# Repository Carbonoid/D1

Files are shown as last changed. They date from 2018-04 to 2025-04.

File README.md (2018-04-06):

## Carbonoid D1
Repository for the Carbonoid D1 Delta Printer

During the development phase and countless optimization iterations 4 machines were built:

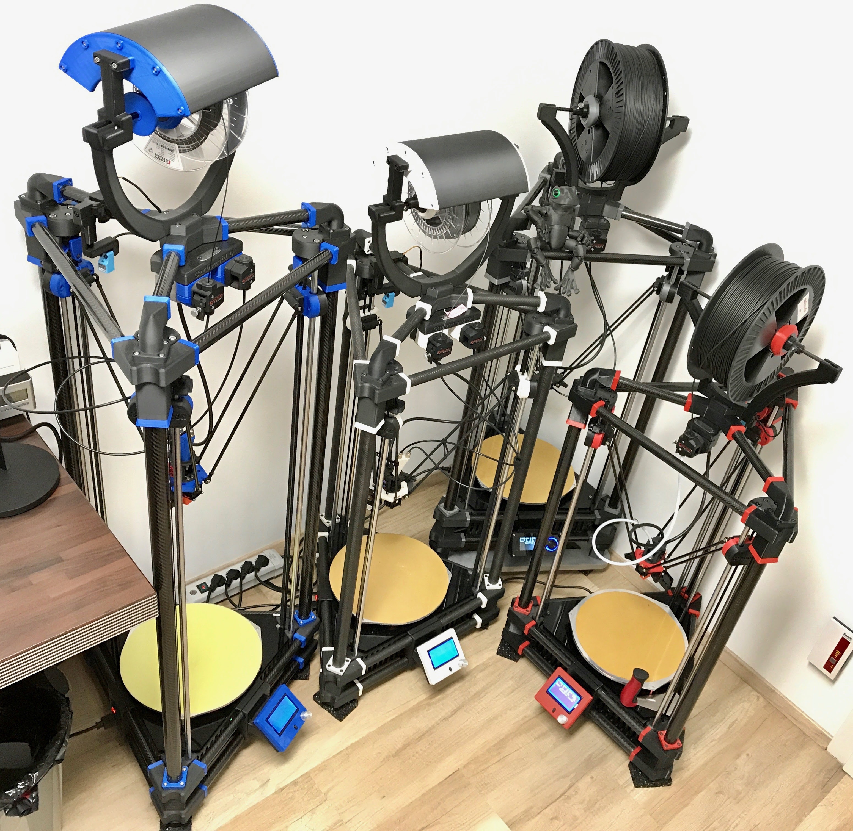
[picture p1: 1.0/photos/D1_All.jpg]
Carbonoid All-stars


The single extrusion machine #0002 is equipped with a Flex3Drive G4 extruder:

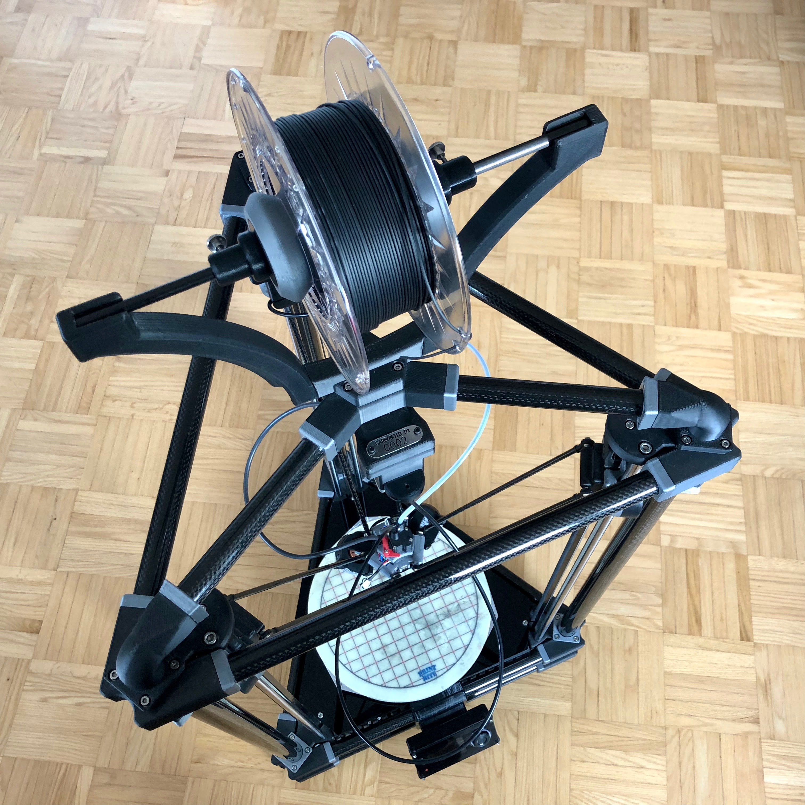
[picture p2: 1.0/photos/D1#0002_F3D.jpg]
Carbonoid D1 #0002 with Flex3Drive extruder


Machine #0004 uses a DuetEthernet and a PanelDue:

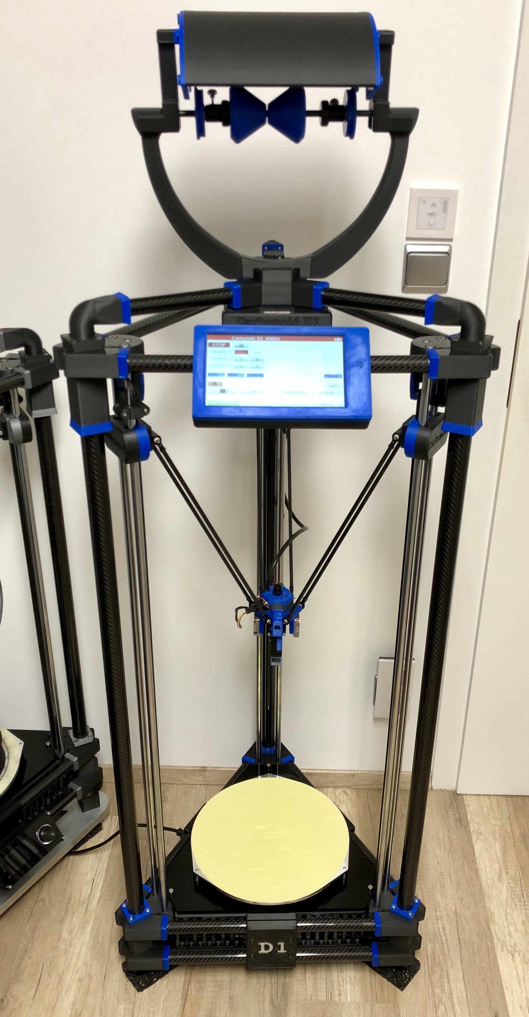
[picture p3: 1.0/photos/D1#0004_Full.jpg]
Carbonoid D1 #0004 Overview


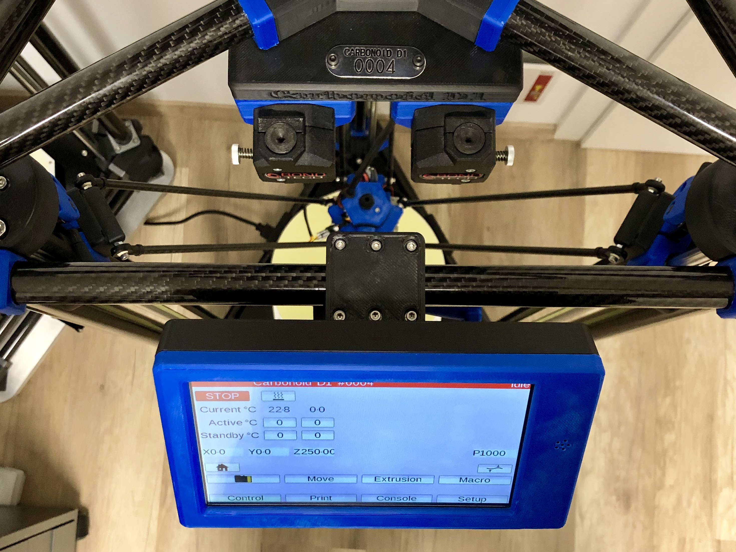
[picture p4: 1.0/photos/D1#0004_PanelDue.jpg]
Carbonoid D1 #0004 Panel Due


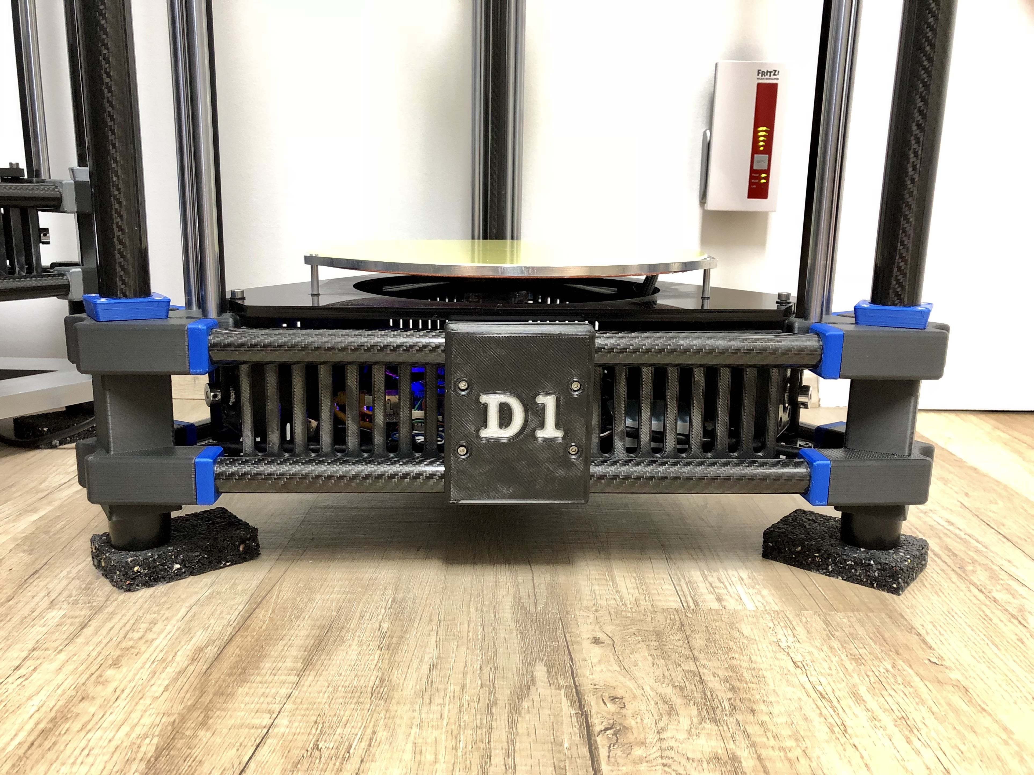
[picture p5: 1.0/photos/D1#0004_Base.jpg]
Carbonoid D1 #0004 Base


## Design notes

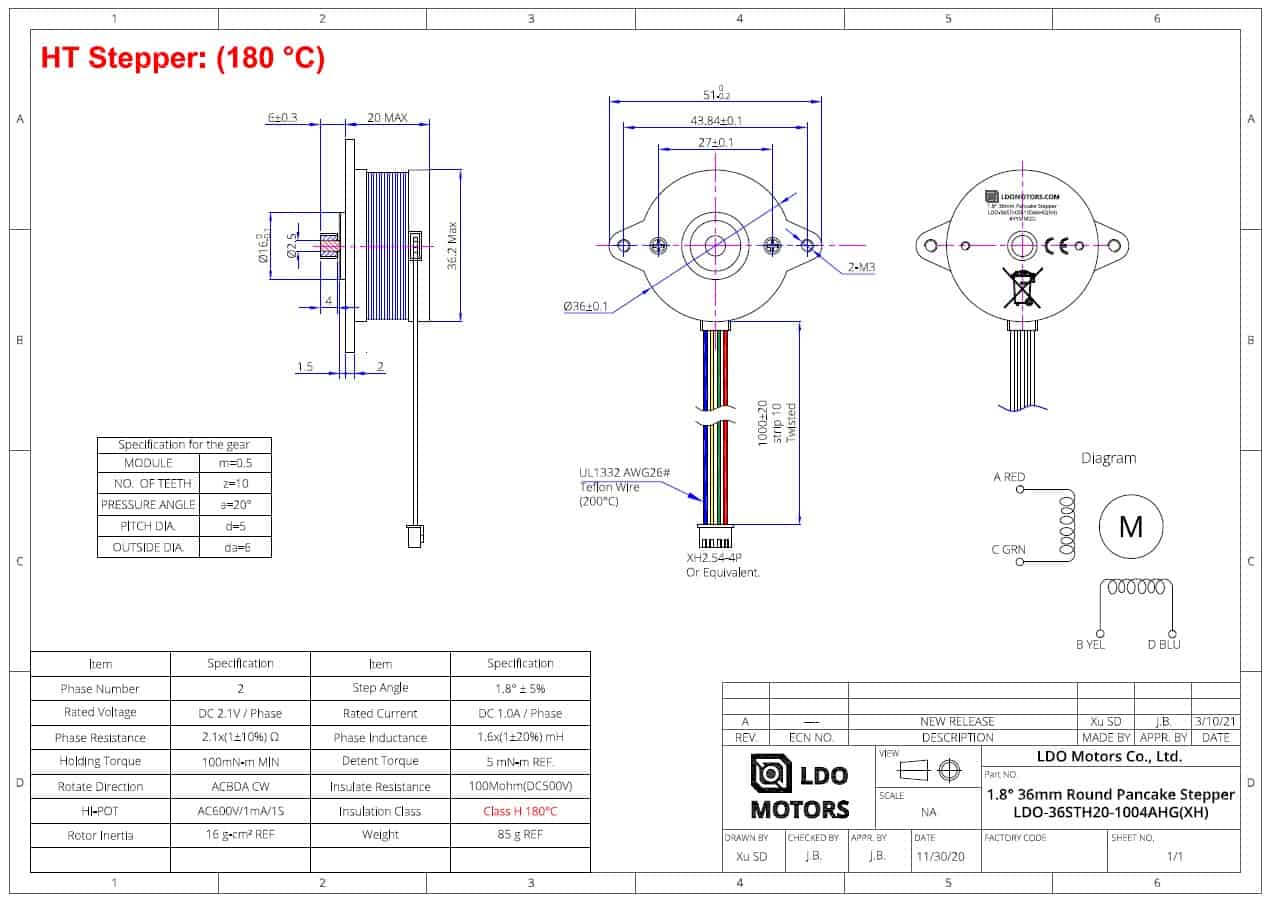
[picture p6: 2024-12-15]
1.0/hardware/drawings_pinouts/Datenblatt_LDO-Motor.jpg

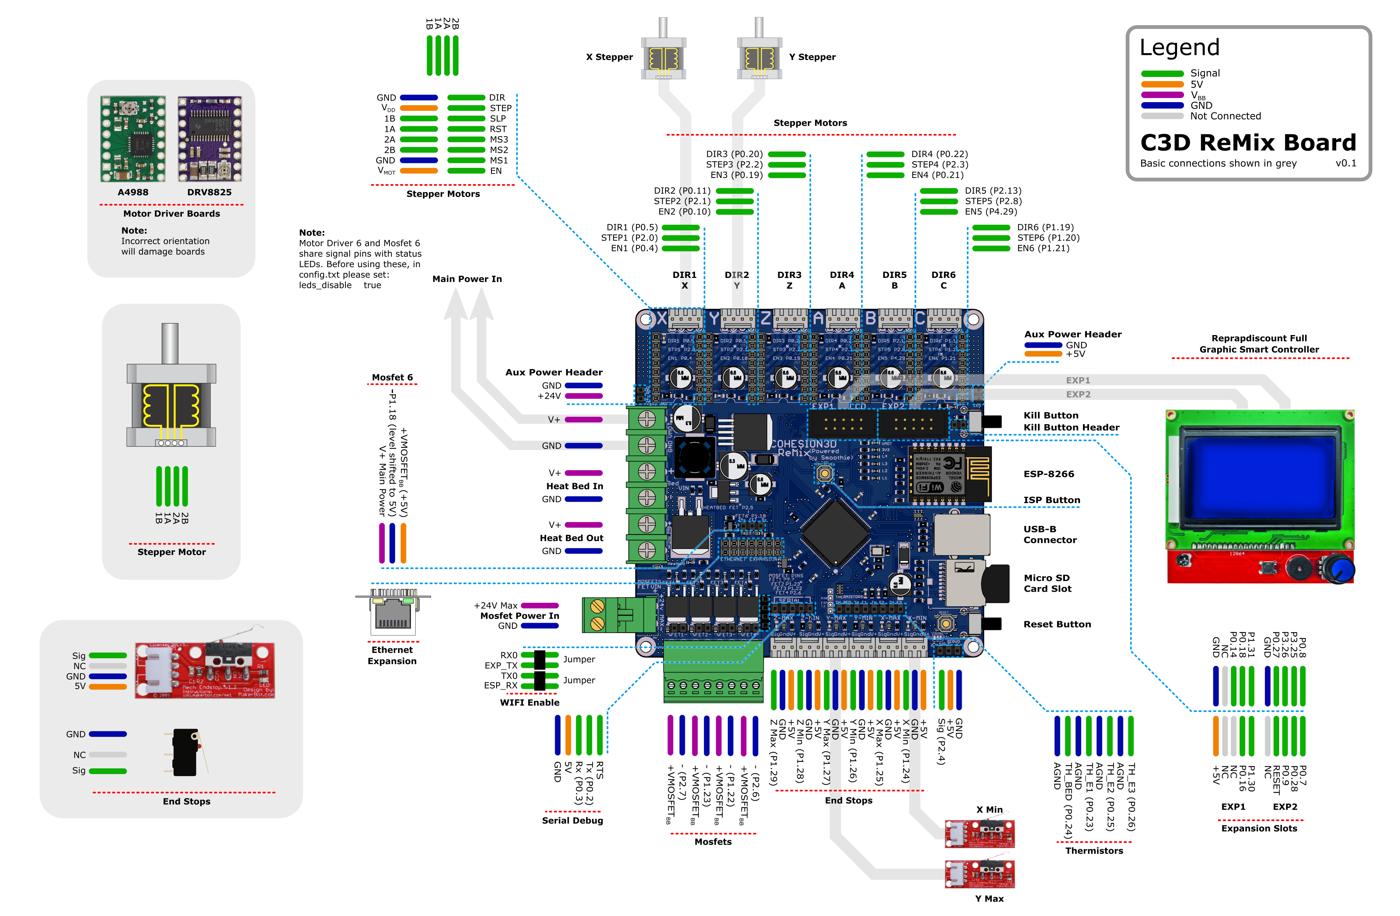
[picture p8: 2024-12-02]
1.0/hardware/drawings_pinouts/C3D_Remix_Pinout.png

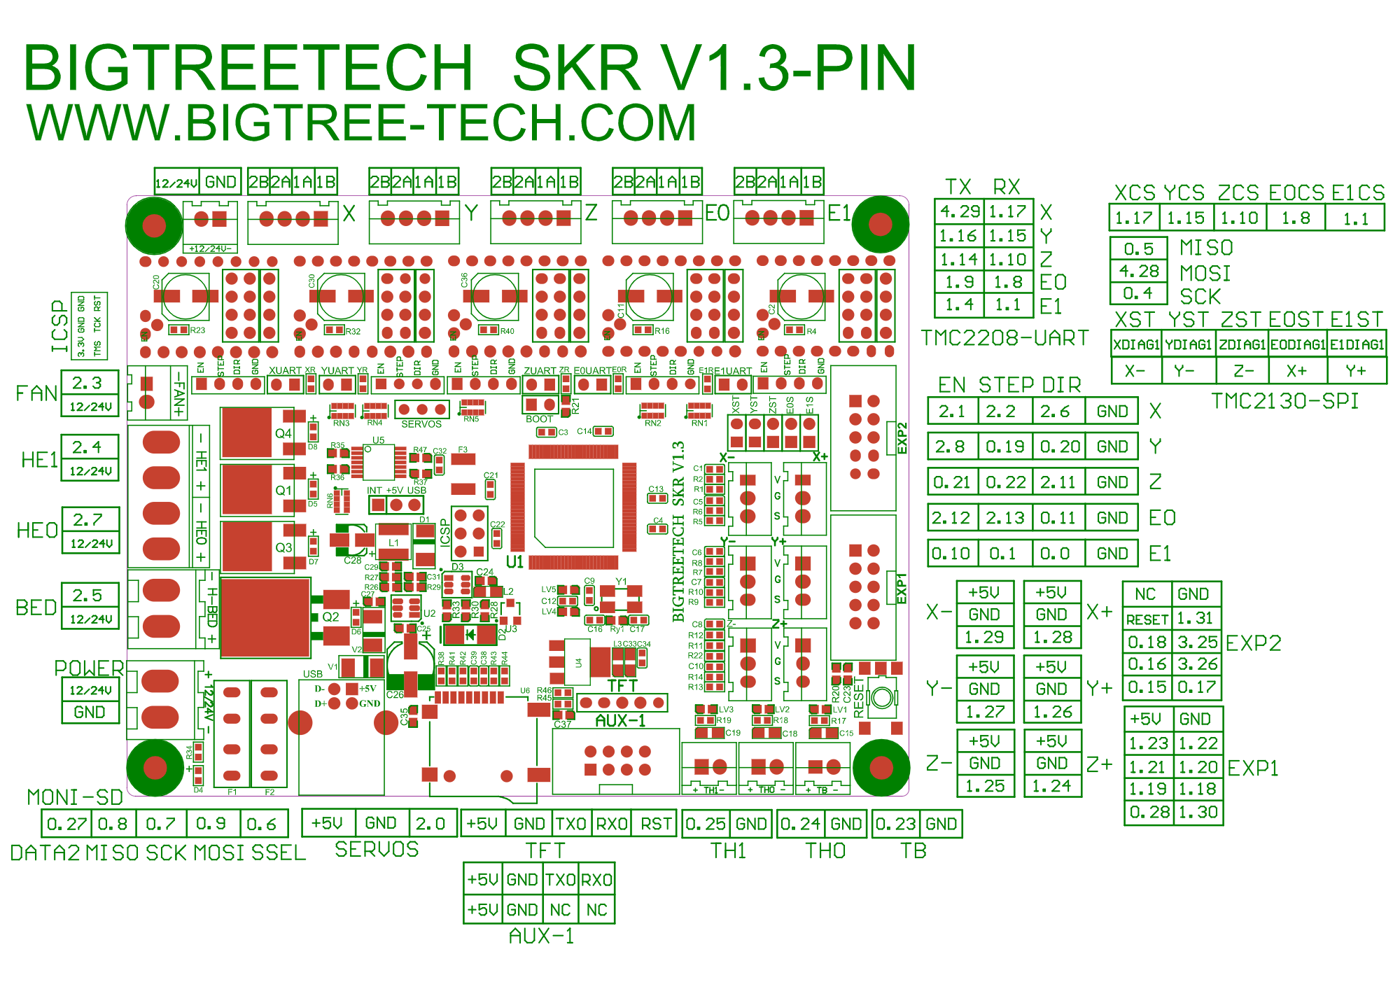
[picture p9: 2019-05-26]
1.0/config_klipper/#0001/BTT_SKR_v1.3_XYZE_TMC2100_F3D_G5/GLCD_Cable/SKR V1.3 Pinout.png

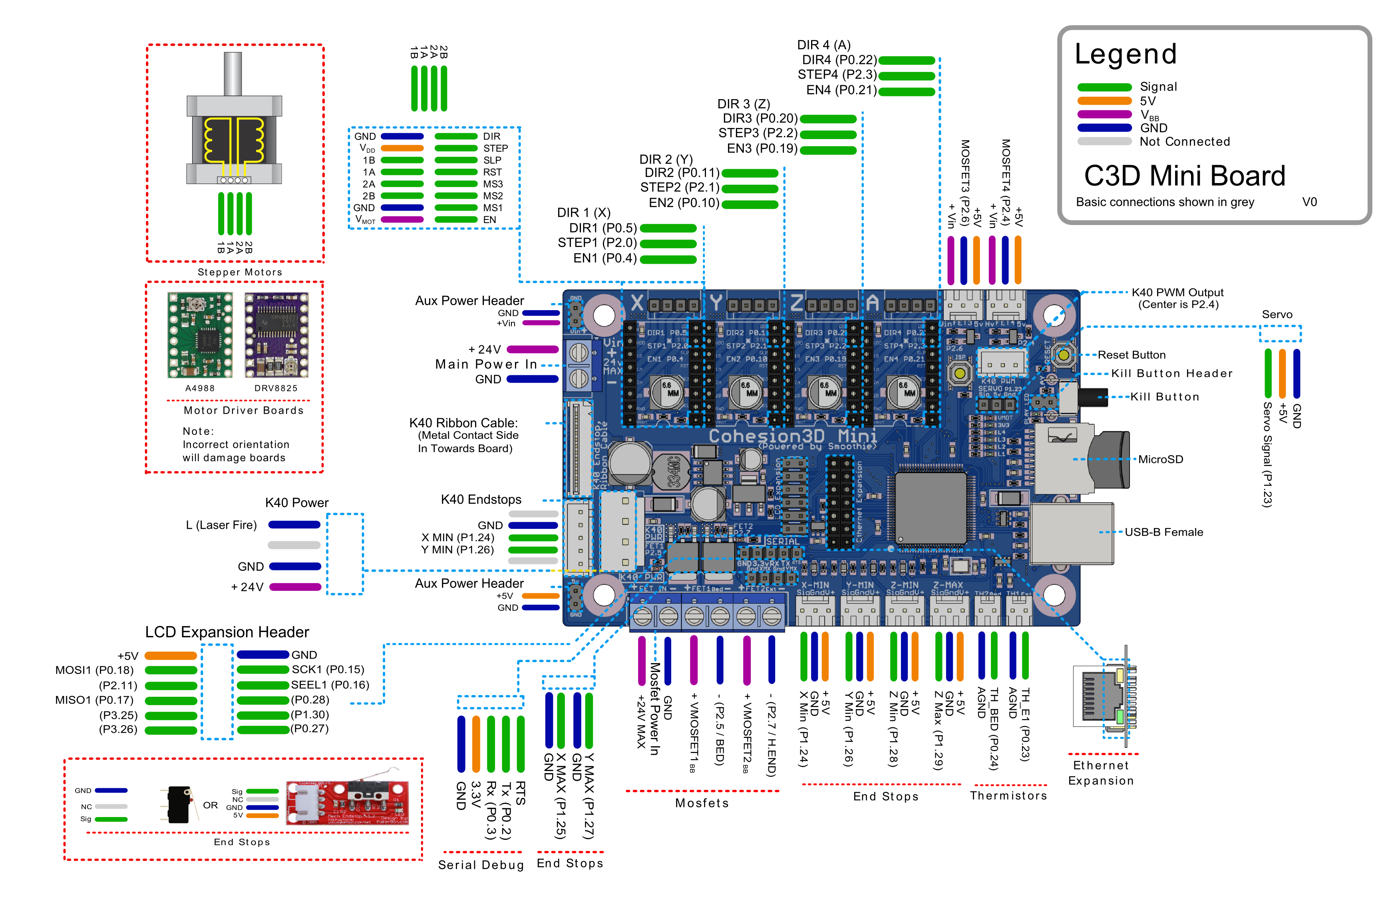
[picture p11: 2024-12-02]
1.0/hardware/drawings_pinouts/C3D_Mini_Pinout.png

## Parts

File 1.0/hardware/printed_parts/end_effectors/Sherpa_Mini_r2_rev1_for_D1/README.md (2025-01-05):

## Sherpa Mini - Release 2 - Carbonoid Specific Changes

No other changes than the ones below were made. The copyright to these files belongs to ANNEX-Engineering: https://github.com/Annex-Engineering/ANNEX-Engineering-License-Agreement

+ Diameter of the 5 heat-set brass inserts modified to 3.8 mm, to match the M3 insert type (Tappex) used on the Carbonoid D1 printer design.

## Sherpa Mini - Release 2:

This release adds support for Bondtech's RIDGA v2 in addition to numerous tweaks and updates to make the extruder easier to work on and more reliable than ever. 

## Changelog

+ Bondtech RIDGA v2 compatibility (R2 RC1 and newer)
+ Bondtech insert support
+ Stronger and stiffer idler arm
+ Increased clearance between idler arm and core
+ Minor fixes and adjustments in preparation for upcoming upgrades

+ Core housing and rear housing need to be reprinted if upgrading from Release 1
+ Updated idler arms are backwards compatible with Release 1 and Release 2 RC1

## FAQ
For Material Requirements, Print Settings and How to Interpret the file naming structure, please see: "Print_Settings_and_File_Key.txt"

The BOM and Sourcing Guide for this product can be found here: https://docs.google.com/spreadsheets/d/1O3eyVuQ6M4F03MJSDs4Z71_XyNjXL5HFTZr1jsaAtRc/edit?usp=sharing

## Product Info
This is the Sherpa Mini Extruder, a ground up design developed by Anlin and the team at Annex Engineering. It's a dual geared hobbed filament extruder designed for use with any printer. It features a gear driven design to provide torque while being able to be near silent. You must perform your own tuning to get the best results.

A Pinion Equipped Pancake Stepper is required for this Release.

Our discord server can be found here: 

Join me on Discord (https://discord.gg/MzTR3zE)

Please only use GitHub Issues for repo and file related problems. For general design related questions and technical support please visit our Discord server.

Image of Sherpa Extruder

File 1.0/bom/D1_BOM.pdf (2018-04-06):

Carbon tubes
Alternative 1 (D1 standard): 3x 30x26x863 mm Alternative 2 (D1 extended): 3x 30x26x1063 mm 9x 22x18x450 mm
3x 22x18x225 mm
6x 6x4x348 mm
Item | Description | Source | Qty.
GT2 Kit | 3x 2m GT2 Zahnriemen, 6x GT2 20 Pulley | www.ebay.de | 1
Shoulder bolts | GMSB4-20 / 34-02-E6 | www.misumi.de | 3
Set Screws | M3x 30 10x | www.ebay.de | 1
Extruder | 1.75 mm Bondtech QR | www.bondtech.se | 1
Silicone bed heater + SSR | 230V / 480W Silikonheizmatte + 230V / 10A SSR www.filafarm.de | 1
PSU | Meanwell RS-100-24 24V/108W | www.ebay.de | 1
Cast aluminium heated bed | 6mm Cast aluminium custom made | http://www.bam-maschinenbau.de | 1
Bearings | F624ZZ | www.ebay.de | 10
Bearings | 604ZZ | www.ebay.de | 4
Alternative 1: Controller / Display | Azteeg X5 mini, mini Viki, 4x SureSepr SD2210 | www.panucatt.com | 1
Alternative 2: Controller / Display | Cohesion3D Remix, GLCD, 4-6x TMC2100/2208 (2208 for xyz and 2100 for extruder works great) www.panucatt.com | 1
Alternative 3: Controller / Display | Cohesion3D mini, GLCD, 4x TMC2100/2208 (2208 for xyz and 2100 for extruder works great) www.panucatt.com | 1
Alternative 4: Controller / Display | Smoothieboard 1.1, GLCD Display | http://smoothieware.org/getting-smoothieboard1
Alternative 5: Controller / Display | DuetEthernet or Wifi, Panel Due 7" | https://www.duet3d.com | 1
Raspberry Pi 3 B+ | Optional but highly recomended | https://www.raspberrypi.org/products/ | 1
SN04 Sensor | SN04-N Sensor | www.aliexpress.com | 1
Filament | 5kg Green-TEC | www.extrudr.com | 1
Ball joints | KBRM-03 M4 MH Igubal ball joint | www.igus.de | 12
Alternative 1: Bushings | 6x Igus RJUM-11-12 | www.igus.de | 6
Alternative 2: Bushings | 6x sintered bronze bushing 16x12x25 mm | www.ebay.de | 6
M2.5 Inserts | KVT M2.5 MULTISERT | http://www.kvt-fastening.de | 6
M3 Insert | KVT M3 MULTISERT | http://www.kvt-fastening.de | 50
M4 Insert normal | KVT M4 MULTISERT | http://www.kvt-fastening.de | 100
M4 Insert long | KVT M4 long MULTISERT | http://www.kvt-fastening.de | 100
M5 Insert | KVT M5 Insert | http://www.kvt-fastening.de | 10
NEMA17 | 0,9° LDO-42STH47-1684MAC.pdf | http://ldomotors.com | 3
Alu Spacer 20mm | Aluminium spacer 20mm | www.aliexpress.com | 3
Alu Spacer 40mm | Aluminium spacer 40mm | www.aliexpress.com | 6
Alternative 1: Linear Rod | 6x 800x12 mm with M6 Threaded Ends | www.dold-mechatronik.de | 1
Alternative 2: Linear Rod | 6x 1000x12 mm with M6 Threaded Ends | www.dold-mechatronik.de | 1
Microswitch | For enstops and alternatively for bed probe | www.ebay.de | 4

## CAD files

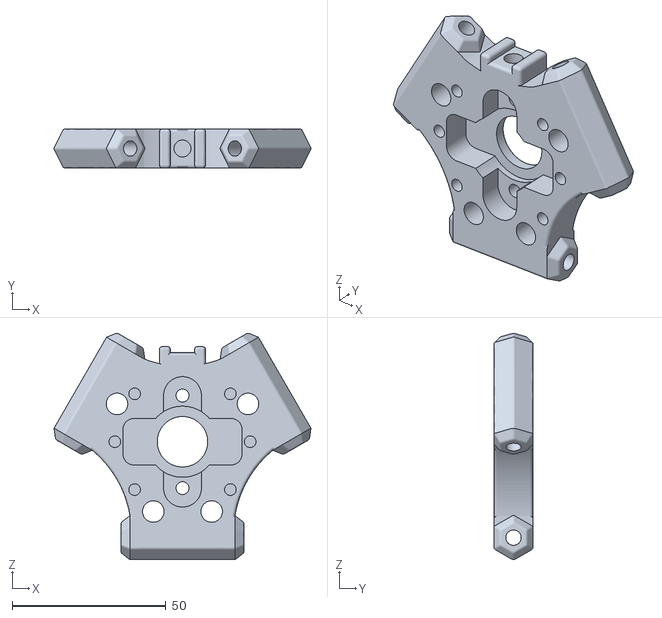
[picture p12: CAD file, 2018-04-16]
1.0/hardware/printed_parts/end_effector_v3.5/end_effector_v3.5.stl
83.5 x 12.7 x 73.6

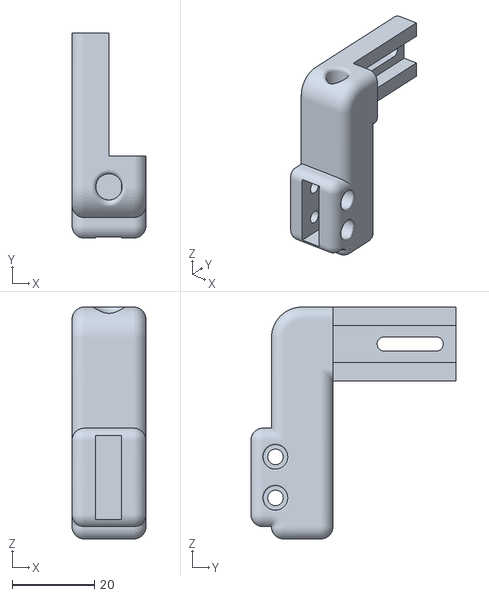
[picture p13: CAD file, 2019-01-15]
1.0/hardware/printed_parts/end_effectors/bed_probe_arm_since_v5/bed_probe_arm_lower_microswitch.stl
18.0 x 50.0 x 56.5

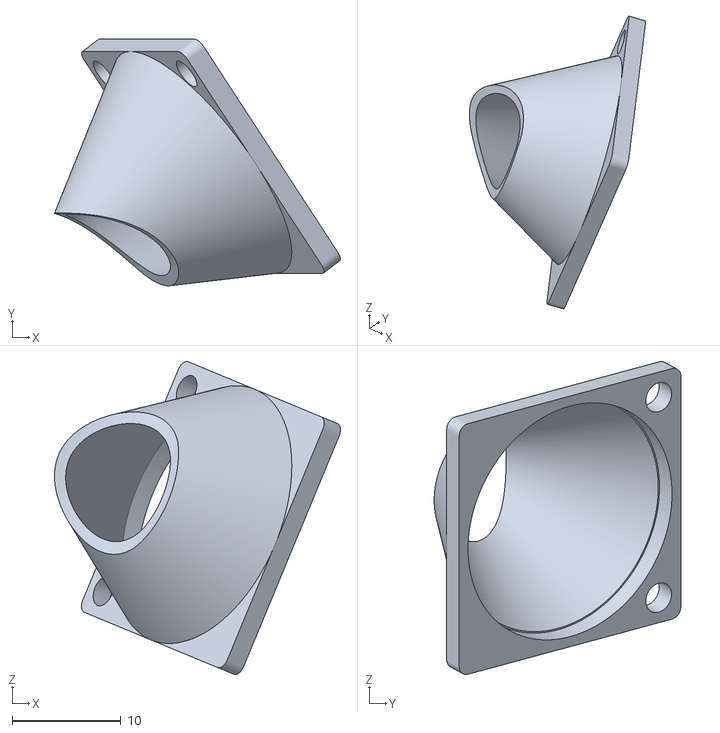
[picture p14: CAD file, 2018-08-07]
1.0/hardware/printed_parts/end_effectors/filament_cooling/25_mm_fan_duct/25_mm_fan_duct.stl
26.4 x 22.7 x 28.8

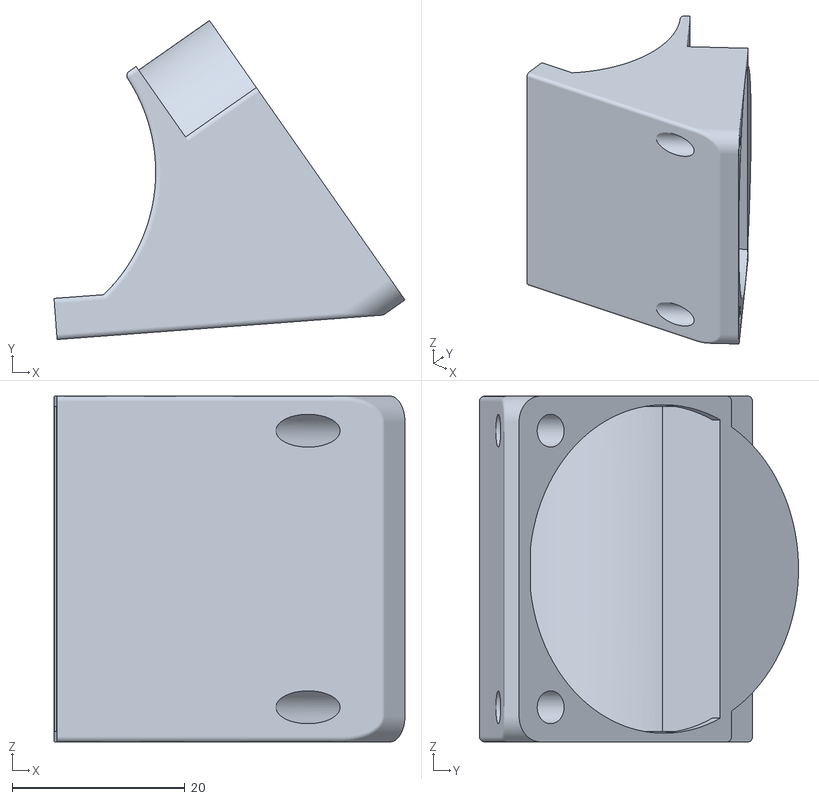
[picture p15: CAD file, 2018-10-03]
1.0/hardware/printed_parts/end_effectors/filament_cooling/40_mm_fan_ducts/40_mm_fan_duct_v5.stl
40.6 x 36.9 x 40.0

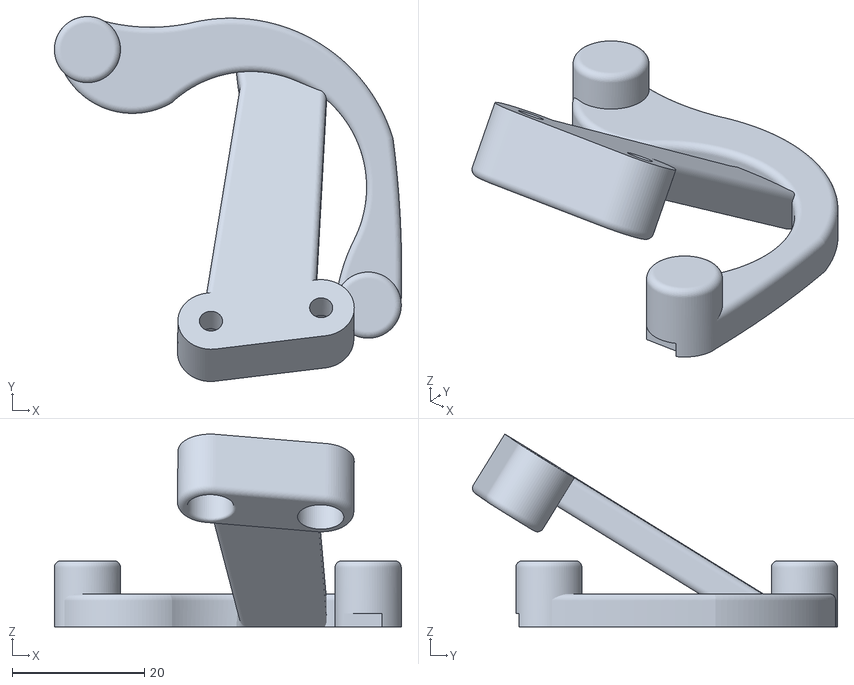
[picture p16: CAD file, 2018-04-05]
1.0/hardware/printed_parts/end_effectors/filament_cooling/double_pabst/pabst_fan_holder.stl
52.5 x 55.2 x 29.1

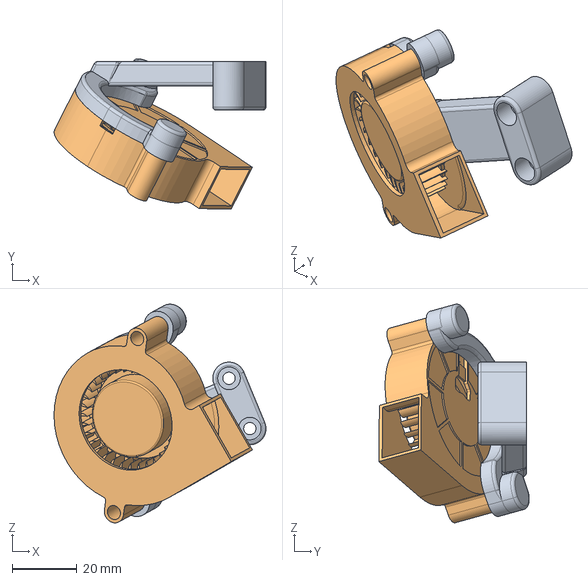
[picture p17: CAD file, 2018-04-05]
1.0/hardware/printed_parts/end_effectors/filament_cooling/single_blower_left/single_blower_left.step
65.6 x 46.5 x 67.6 mm
BlowerFanHolder
50mm Blower Fan

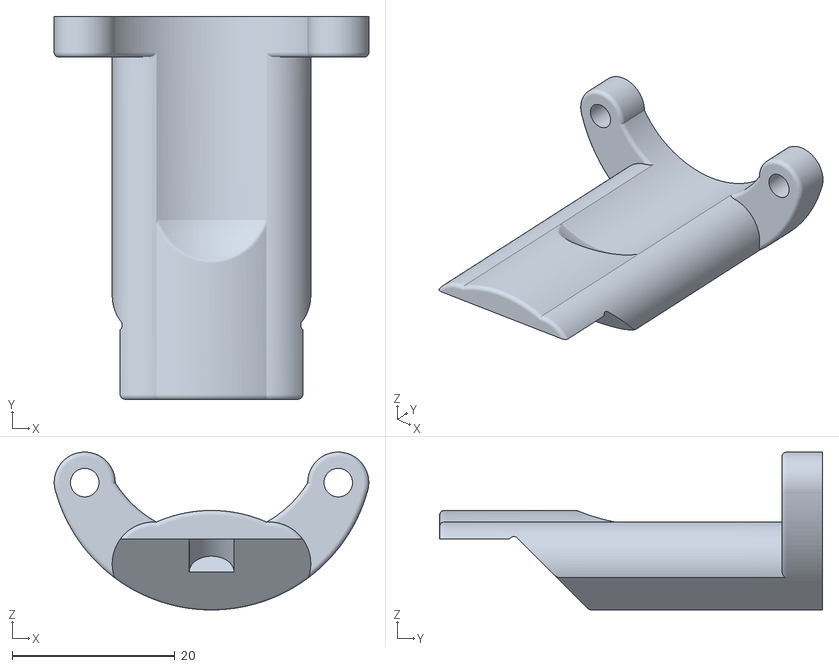
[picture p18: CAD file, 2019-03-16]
1.0/hardware/printed_parts/end_effectors/filament_cooling/single_pabst/pabst_nozzle_holder_long_mk12.stl
38.6 x 47.0 x 19.4

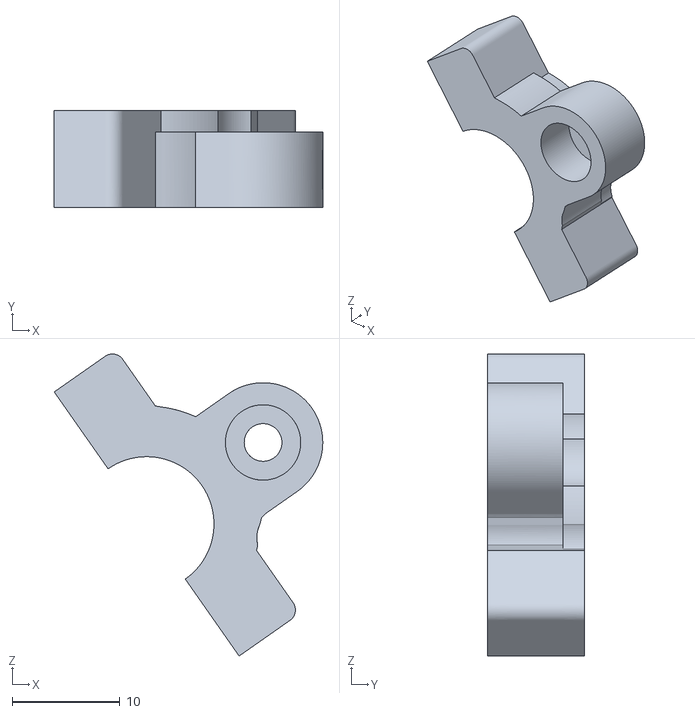
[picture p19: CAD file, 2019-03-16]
1.0/hardware/printed_parts/end_effectors/hot_end_adapters_since_v5/dyzend-x/dyzend-x_adapter_back.stl
24.9 x 9.00 x 28.1

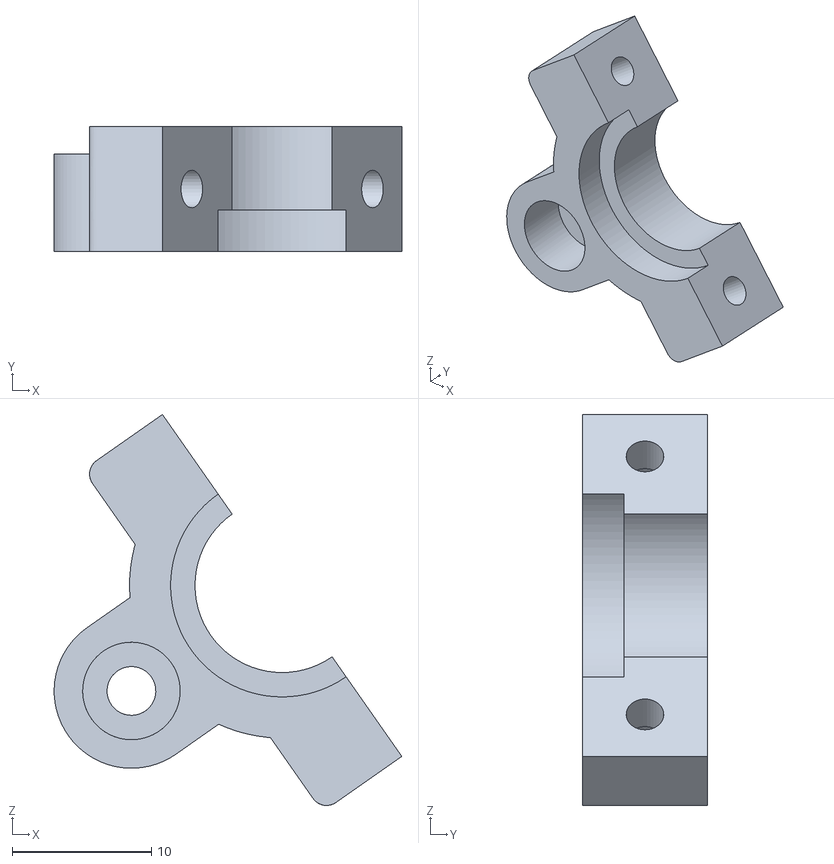
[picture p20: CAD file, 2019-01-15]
1.0/hardware/printed_parts/end_effectors/hot_end_adapters_since_v5/e3d/e3d_adapter_front.stl
24.9 x 9.00 x 28.1

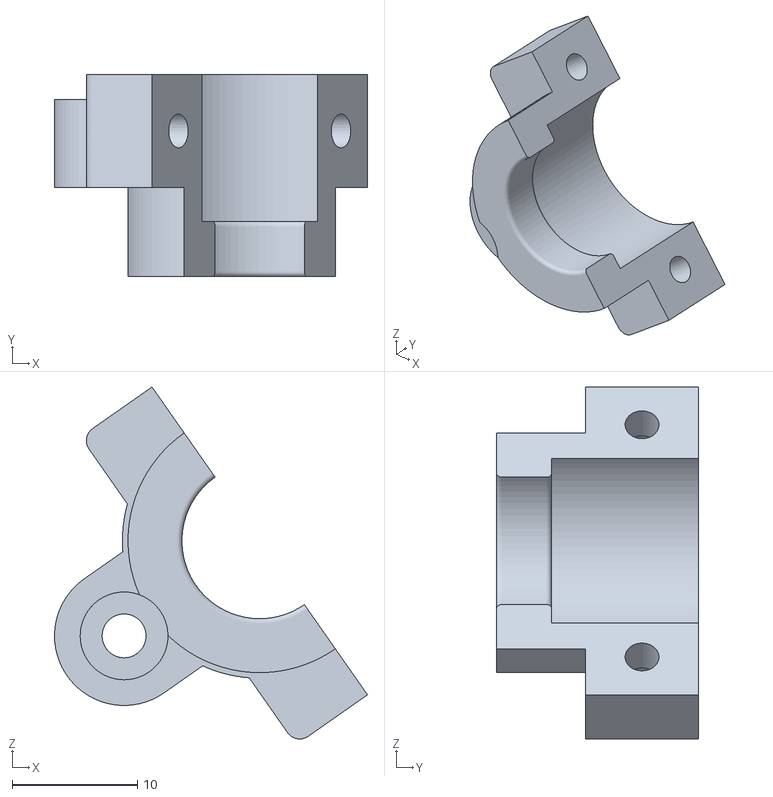
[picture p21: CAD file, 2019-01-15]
1.0/hardware/printed_parts/end_effectors/hot_end_adapters_since_v5/j_head/j_head_adapter_front.stl
24.9 x 16.1 x 28.1

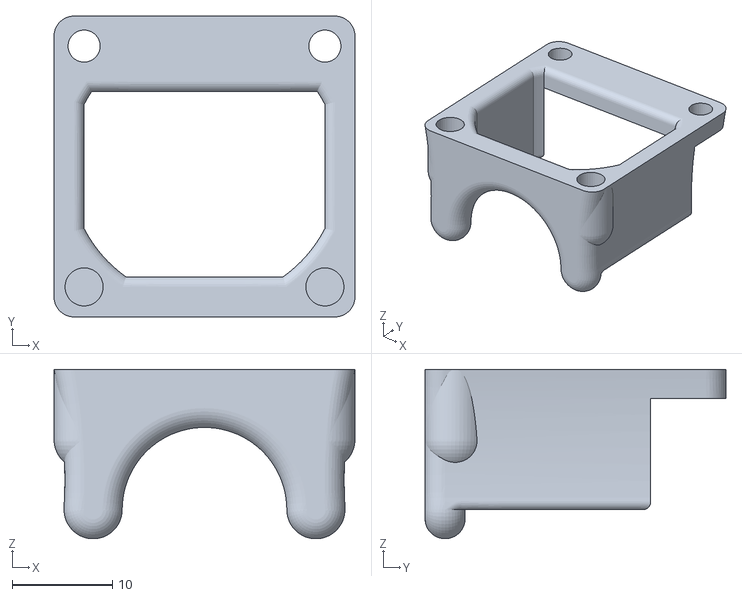
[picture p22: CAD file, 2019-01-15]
1.0/hardware/printed_parts/end_effectors/hot_end_adapters_since_v5/j_head/j_head_fan_duct/j_head_fan_duct_30_mm.stl
30.0 x 30.0 x 16.9

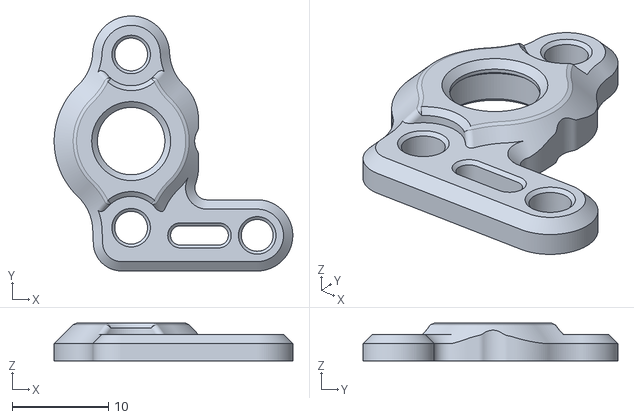
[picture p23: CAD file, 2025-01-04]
1.0/hardware/printed_parts/end_effectors/Sherpa_Mini_r2_rev1_for_D1/housing_front.stl
24.8 x 26.5 x 3.90

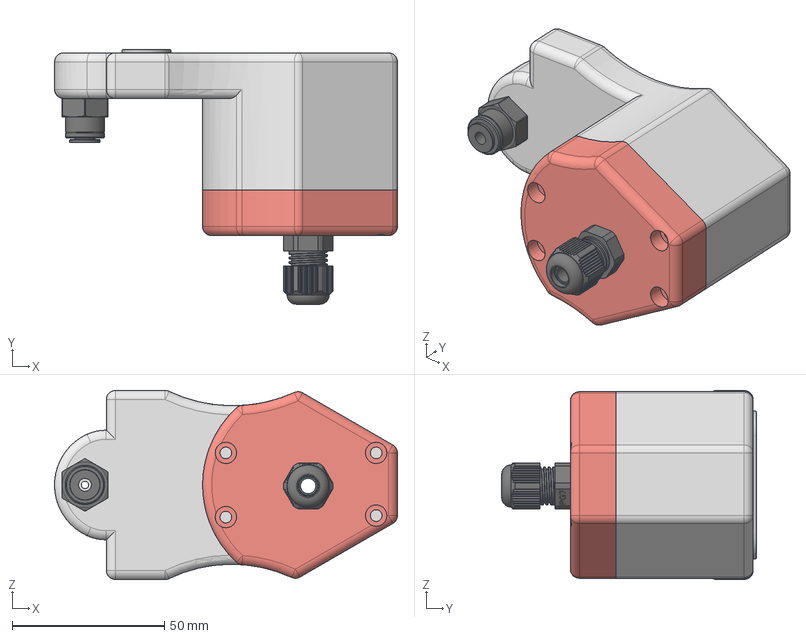
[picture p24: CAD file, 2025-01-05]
1.0/hardware/printed_parts/end_effectors/v10/electric_compartment/electronic_compartment_orbiter.step
112.5 x 83.5 x 62.0 mm
D1_Orbiter_Electronic_Box
Durchführung_PG7
PushFit_JG_PM010401E
TypePlate

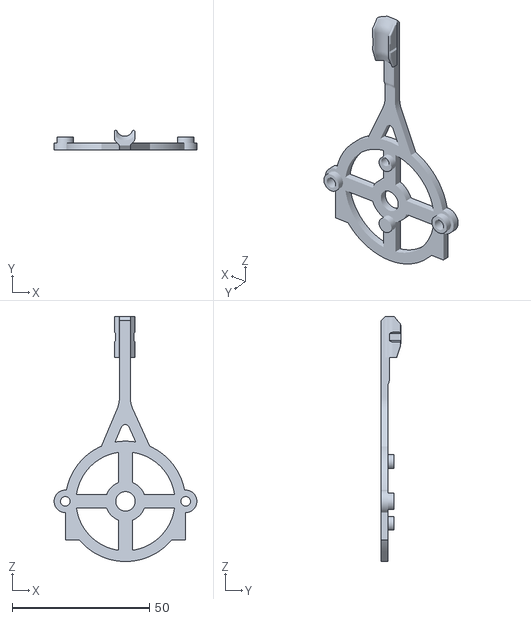
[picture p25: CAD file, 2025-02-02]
1.0/hardware/printed_parts/end_effectors/v10/WirerestrainBracketEBB36.stl
52.0 x 7.13 x 89.2

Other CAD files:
1.0/hardware/printed_parts/end_effectors/v6.x/electric_compartment/electric_compartment_base_for_v6.x.stl
1.0/hardware/printed_parts/end_effectors/v6.x/end_effector_v6.5/end_effector_v6.5.step
1.0/hardware/printed_parts/end_effectors/v8-v9/electric_compartment_top_f3d_g4.stl
1.0/hardware/printed_parts/frame/base_plate/base_plate.step
1.0/hardware/printed_parts/end_effector_v3.5/end_effector_v3.5.f3d
1.0/hardware/printed_parts/end_effector_v3/adapters/dyzend-x/clip_dyzend-x_back.stl
1.0/hardware/printed_parts/end_effector_v3/adapters/dyzend-x/clip_dyzend-x_front.stl
1.0/hardware/printed_parts/end_effector_v3/adapters/e3d/clip_e3d_v6_back.stl
1.0/hardware/printed_parts/end_effector_v3/adapters/e3d/clip_e3d_v6_front.stl
1.0/hardware/printed_parts/end_effector_v3/adapters/j-head/clip_j-head_back.stl
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

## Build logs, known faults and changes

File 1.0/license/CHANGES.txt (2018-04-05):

Modifications made by Licensee (see section 3.4.b in OHL):
==========================================================

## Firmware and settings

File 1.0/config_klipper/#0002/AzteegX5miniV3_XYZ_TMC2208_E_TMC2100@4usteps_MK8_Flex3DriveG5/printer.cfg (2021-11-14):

# ============================================ #
# Klipper configuration for Carbonoid D1 #0002 #
# ============================================ #
# Controller Board: Panucat Azteeg X5 mini V3  #
# Steppers XYZ:     TMC2208 @ 16 usteps        #
# Stepper E:        TMC2100 @ 4 usteps         #
# Compile Target:   LPC176x (120MHz)           #
# ============================================ #

[mcu]
serial: /dev/serial/by-id/usb-Klipper_lpc1769_1000010FC384C8AE42E3C156C22000F5-if00 
baud: 250000

##################
# Delta specific #
##################

[printer]
kinematics: delta
max_velocity: 500
max_accel: 2400
max_z_velocity: 200
minimum_z_position: 0 # -5 during probing
#delta_radius: 140

[delta_calibrate]
radius: 140
horizontal_move_z: 5 # 30 with probe else 5

[probe]
pin: !P1.29
z_offset: 30  # 30 with probe. The distance (in mm) between the bed and the nozzle when the probe triggers
speed: 5.0    # Speed (in mm/s) of the Z axis when probing. The default is 5mm/s.

########################################
# Tower motors & enstops configuration #
########################################

[stepper_a]
step_pin: P2.1
dir_pin: !P0.11
enable_pin: !P0.10
#step_distance: .00625
endstop_pin: !P1.24
microsteps: 16
rotation_distance: 40
#position_endstop: 267.50
homing_speed: 33
#arm_length: 366.50

[stepper_b]
step_pin: P2.2
dir_pin: !P0.20
enable_pin: !P0.19
#step_distance: .00625
endstop_pin: !P1.26
microsteps: 16
rotation_distance: 40

[stepper_c]
step_pin: P2.3
dir_pin: !P0.22
enable_pin: !P0.21
#step_distance: .00625
endstop_pin: !P1.28
microsteps: 16
rotation_distance: 40

##################################################
# Extruder, hot-end &  hot-end fan configuration #
##################################################

[extruder]
# Flex3Drive
gear_ratio: 40:1
full_steps_per_rotation: 200
rotation_distance: 30.7818 
#@8 microsteps
step_pin: P2.0
dir_pin: P0.5
enable_pin: !P0.4
microsteps: 4
# 10,52631579 / 625 * 40 = 0,6736842106
# rotation_distance: 0.6736842106
nozzle_diameter: 0.400
filament_diameter: 1.750
max_extrude_only_velocity: 30
max_extrude_only_accel: 150
max_extrude_only_distance: 1000
heater_pin: P2.5
sensor_type: Honeywell 100K 135-104LAG-J01
sensor_pin: P0.24
control: pid
pid_Kp: 26.4
pid_Ki: 1.437
pid_Kd: 121
min_temp: 0
max_temp: 250

[heater_fan extruder_fan]
pin: P0.26
max_power: 1.0
heater: extruder
heater_temp: 50.0
fan_speed: 1.0

# Print cooling fan
[fan]
pin: P1.25

#########################
# Heatbed configuration #
#########################

[heater_bed]
heater_pin: P2.7
sensor_type: EPCOS 100K B57560G104F
sensor_pin: P0.23
#control: watermark
min_temp: 0
max_temp: 130

##########################################################
# "Panucatt Viki 2 128x64 Full Graphic Smart Controller" #
##########################################################
[display]
lcd_type: uc1701
cs_pin: P0.16
a0_pin: P2.6
encoder_pins: ^!P3.25, ^P3.26
click_pin: ^!P2.11
contrast: 63

[output_pin beeper]
pin: P0.25

#*# <---------------------- SAVE_CONFIG ---------------------->
#*# DO NOT EDIT THIS BLOCK OR BELOW. The contents are auto-generated.
#*#
#*# [printer]
#*# delta_radius = 164.268022
#*#
#*# [stepper_a]
#*# angle = 210.532530
#*# arm_length = 366.500000
#*# position_endstop = 273.353031
#*#
#*# [stepper_b]
#*# angle = 329.784149
#*# arm_length = 366.500000
#*# position_endstop = 273.883332
#*#
#*# [stepper_c]
#*# angle = 90.000000
#*# arm_length = 366.500000
#*# position_endstop = 273.744610
#*#
#*# [delta_calibrate]
#*# height0 = 0.0
#*# height0_pos = 21860.000,21907.000,21902.000
#*# height1 = 0.0
#*# height1_pos = 27288.000,27313.000,18889.000
#*# height2 = 0.0
#*# height2_pos = 21327.000,30259.000,21339.000
#*# height3 = 0.0
#*# height3_pos = 18970.000,26406.000,26415.000
#*# height4 = 0.0
#*# height4_pos = 21071.000,21130.000,27662.000
#*# height5 = 0.0
#*# height5_pos = 25548.000,19171.000,25619.000
#*# height6 = 0.0
#*# height6_pos = 28837.000,21227.000,21210.000
#*#
#*# [heater_bed]
#*# control = pid
#*# pid_kp = 40.846
#*# pid_ki = 2.017
#*# pid_kd = 206.782

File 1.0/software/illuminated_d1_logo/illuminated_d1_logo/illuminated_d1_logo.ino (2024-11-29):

/*
  Illuminated D1 Logo
  
  Using a NeoPixel module to illumniate the Carbonoid D1 Logo Panel.
  
  Created by:  Alex Skoruppa
  Date:        May 10, 2019
  License:     GPLv3
*/
#include <Adafruit_NeoPixel.h>

#define PIN            2
#define NUMPIXELS      7
 
Adafruit_NeoPixel pixels = Adafruit_NeoPixel(NUMPIXELS, PIN, NEO_GRB + NEO_KHZ800);
  
void setup() {
  pixels.begin();
  randomSeed(analogRead(0));
  Serial.begin(9600);
}

void set_all_pixels(byte r, byte g, byte b)
{    
  for(int i=0;i<NUMPIXELS;i++)
  {
    pixels.setPixelColor(i, pixels.Color(r, g, b)); // Moderately bright green color.
    pixels.show(); // This sends the updated pixel color to the hardware.
  }  
}

void turn_off_all_pixels()
{
  for(int i=0;i<NUMPIXELS;i++)
  {
    pixels.setPixelColor(i, pixels.Color(0,0,0)); // Moderately bright green color.
    pixels.show(); // This sends the updated pixel color to the hardware.
  } 
}

void dim_on_all_pixels(byte r, byte g, byte b, int delay_t)
{
  for(int i=0;i<255;i++)
  {
     set_all_pixels(r/255.*i,g/255.*i,b/255.*i);
     delay(delay_t); // Delay for a period of time (in milliseconds).
  }  
}

void dim_off_all_pixels(byte r, byte g, byte b, int delay_t)
{
  for(int i=255;i>-1;i--)
  {
     set_all_pixels(r/255.*i,g/255.*i,b/255.*i);
     delay(delay_t); // Delay for a period of time (in milliseconds).
  }  
}

void loop() {
 
  byte r = random(0, 255);
  byte g = random(0, 255);
  byte b = random(0, 255);
  
  /*String message = "R:"+ String(r) + " G:" + String(g) + " B:" + String(b);
  Serial.println(message);//*/

  int color_change_delay_ms = 15;
  
  dim_on_all_pixels(r,g,b,color_change_delay_ms);
  dim_off_all_pixels(r,g,b,color_change_delay_ms);
}

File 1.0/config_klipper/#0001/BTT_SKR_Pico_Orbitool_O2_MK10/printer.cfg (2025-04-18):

# ============================================ #
# Klipper configuration for Carbonoid D1 #0001 #
# ============================================ #
# Controller Board: SKR Pico                   #
# Steppers XYZ:     TMC2209 @ 16 usteps        #
# Compile Target:   RP2040 (133MHz)            #
# ============================================ #
[mcu]
# USB serial string: SKR_Pico_D1_0001
serial: /dev/serial/by-id/usb-Klipper_rp2040_SKR_Pico_D1_0001-if00
restart_method: command

#######################################
# Extruder specific in external file: #
#######################################
[include orbitool_o2.cfg]

[printer]
kinematics: delta
max_velocity: 500
max_accel: 2400
max_z_velocity: 200
minimum_z_position: -5 # -5 during probing
#delta_radius: 140

[delta_calibrate]
radius: 135
# uncomment before probing with microswitch probe
horizontal_move_z: 30


[stepper_a]
step_pin: gpio11
dir_pin: gpio10
enable_pin: !gpio12
microsteps: 16
rotation_distance: 20
endstop_pin: !gpio4
homing_speed: 50
#position_endstop: 240
#arm_length: 315


[tmc2209 stepper_a]
uart_pin: gpio9
tx_pin: gpio8
uart_address: 0
run_current: 0.7
stealthchop_threshold: 0 # stealthchop OFF run in spread-cycle mode


[stepper_b]
step_pin: gpio6
dir_pin: gpio5
enable_pin: !gpio7
microsteps: 16
rotation_distance: 20
endstop_pin: !gpio3

[tmc2209 stepper_b]
uart_pin: gpio9
tx_pin: gpio8
uart_address: 2
run_current: 0.7
stealthchop_threshold: 0 # stealthchop OFF run in spread-cycle mode

[stepper_c]
step_pin: gpio19
dir_pin: gpio28
enable_pin: !gpio2
microsteps: 16
rotation_distance: 20
endstop_pin: !gpio25

[tmc2209 stepper_c]
uart_pin: gpio9
tx_pin: gpio8
uart_address: 1
run_current: 0.7
stealthchop_threshold: 0 # stealthchop OFF run in spread-cycle mode

[heater_bed]
heater_pin: gpio21
sensor_type: NTC 100K MGB18-104F39050L32
sensor_pin: gpio26
#control: watermark
min_temp: 0
max_temp: 150

[neopixel board_rgb]
pin: gpio24
chain_count: 1
color_order: GRB
initial_RED: 0.0
initial_GREEN: 0.0
initial_BLUE: 0.0

[virtual_sdcard]
path: ~/printer_data/gcodes

[display_status]

[pause_resume]

[gcode_macro PAUSE]
description: Pause the actual running print
rename_existing: PAUSE_BASE
# change this if you need more or less extrusion
variable_extrude: 1.0
gcode:
  ##### read E from pause macro #####
  {% set E = printer["gcode_macro PAUSE"].extrude|float %}
  ##### set park positon for x and y #####
  # default is your max posion from your printer.cfg
  {% set x_park = printer.toolhead.axis_maximum.x|float - 5.0 %}
  {% set y_park = printer.toolhead.axis_maximum.y|float - 5.0 %}
  ##### calculate save lift position #####
  {% set max_z = printer.toolhead.axis_maximum.z|float %}
  {% set act_z = printer.toolhead.position.z|float %}
  {% if act_z < (max_z - 2.0) %}
      {% set z_safe = 2.0 %}
  {% else %}
      {% set z_safe = max_z - act_z %}
  {% endif %}
  ##### end of definitions #####
  PAUSE_BASE
  G91
  {% if printer.extruder.can_extrude|lower == 'true' %}
    G1 E-{E} F2100
  {% else %}
    {action_respond_info("Extruder not hot enough")}
  {% endif %}
  {% if "xyz" in printer.toolhead.homed_axes %}
    G1 Z{z_safe} F900
    G90
    G1 X{x_park} Y{y_park} F6000
  {% else %}
    {action_respond_info("Printer not homed")}
  {% endif %} 

[gcode_macro RESUME]
description: Resume the actual running print
rename_existing: RESUME_BASE
gcode:
  ##### read E from pause macro #####
  {% set E = printer["gcode_macro PAUSE"].extrude|float %}
  #### get VELOCITY parameter if specified ####
  {% if 'VELOCITY' in params|upper %}
    {% set get_params = ('VELOCITY=' + params.VELOCITY)  %}
  {%else %}
    {% set get_params = "" %}
  {% endif %}
  ##### end of definitions #####
  {% if printer.extruder.can_extrude|lower == 'true' %}
    G91
    G1 E{E} F2100
  {% else %}
    {action_respond_info("Extruder not hot enough")}
  {% endif %}  
  RESUME_BASE {get_params}

[gcode_macro CANCEL_PRINT]
description: Cancel the actual running print
rename_existing: CANCEL_PRINT_BASE
gcode:
  G28
  TURN_OFF_HEATERS
  M107
  CANCEL_PRINT_BASE

[gcode_macro HOTEND_PID_TUNE]
description: Runs PID calibration for the extruder hotend.
gcode:
  PID_CALIBRATE HEATER=extruder TARGET=220

[gcode_macro BED_PID_TUNE]
description: Runs PID calibration for the heated bed.
gcode:
  PID_CALIBRATE HEATER=heater_bed TARGET=120

[gcode_macro MANUAL_DELTA_CALIBRATION]
description: Runs the manual delta calibration sequence (paper test).
gcode:
  G28
  DELTA_CALIBRATE METHOD=manual

#*# <---------------------- SAVE_CONFIG ---------------------->
#*# DO NOT EDIT THIS BLOCK OR BELOW. The contents are auto-generated.
#*#
#*# [heater_bed]
#*# control = pid
#*# pid_kp = 57.783
#*# pid_ki = 2.713
#*# pid_kd = 307.695
#*#
#*# [extruder]
#*# control = pid
#*# pid_kp = 15.179
#*# pid_ki = 0.606
#*# pid_kd = 95.061
#*#
#*# [printer]
#*# delta_radius = 154.386306
#*#
#*# [stepper_a]
#*# angle = 210.090613
#*# arm_length = 315.000000
#*# position_endstop = 244.769272
#*#
#*# [stepper_b]
#*# angle = 329.733921
#*# arm_length = 315.000000
#*# position_endstop = 244.213422
#*#
#*# [stepper_c]
#*# angle = 90.000000
#*# arm_length = 315.000000
#*# position_endstop = 244.509476
#*#
#*# [delta_calibrate]
#*# height0 = 0.0
#*# height0_pos = 39146.000,39032.000,39167.000
#*# height1 = 0.0
#*# height1_pos = 51300.000,51240.000,32828.000
#*# height2 = 0.0
#*# height2_pos = 37981.000,58589.000,38028.000
#*# height3 = 0.0
#*# height3_pos = 33080.000,49161.000,49311.000
#*# height4 = 0.0
#*# height4_pos = 37570.000,37427.000,52193.000
#*# height5 = 0.0
#*# height5_pos = 47489.000,33301.000,47484.000
#*# height6 = 0.0
#*# height6_pos = 55169.000,37630.000,37756.000

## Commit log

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2018-04-07 Added design for spool holder cone and stopper.
    [spool_holder_cone.f3d, spool_holder_cone.iges, spool_holder_cone.step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]
2018-04-07 Fixed directory name
    [spool_holder_cone.f3d, spool_holder_cone.iges, spool_holder_cone.step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]
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2018-04-16 Added end effector design V3.5
    Design is easier to print but compatible to V3. It prints nicely without support @0.15 mm layer height and high infill rate (66% recomended).
    [end_effector_v3.5.f3d, end_effector_v3.5.stl]
2018-07-21 Added cover for dual extruder holder covering one motor mount point.
    [no_motor_cover.stl]
2018-07-21 Updated extruder holders with cover for one motor mount point.
    [extruder_holders.f3d, extruder_holders.iges, extruder_holders.step]
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2018-08-07 Added STLs for a 25 mm fan duct and holder for filament cooling
    [25_mm_fan_duct.stl, fan_holder_25_mm.stl]
2018-08-18 Updated config after installing a silicone sock on the J-Head MK10
    [40_mm_fan_duct_v2.stl]
2018-08-19 Added design V2 of filament cooling based on 40 mm fans
    [40_mm_fan_duct.stl, 40_mm_fan_duct_big_cutout.stl, 40_mm_fan_ducts.f3d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]
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2019-02-17 Updated electronic compartments
    Updates to V6.x an V7 electronic compartments:
    - Top parts for Flex3Drives were reduced in height by 2.8 mm
    - New top parts for Flex3Drive G5
    [electric_compartment_for_v6.x.f3d, electric_compartment_for_v7.f3d, electric_compartment_top_f3d_g4_for_v6.x.stl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]
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2019-03-16 Updated design of single pabst blower fan duct
    - Added shorter version of the holder part for DynEND-X hotend
    - Added longer version for J-Head MK12 HiFlow hotend
    [pabst_blower_fan.f3d, pabst_holder_j-head_e3d_v6.stl, pabst_nozzle_holder_long_mk12.stl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]
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2019-05-26 Added fotos of expansion slots with connected workaround cable.
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2019-05-26 Changed XYZ Stepper Drivers
    Switched XYZ drivers from TMC2208 to TMC2100, the TMC2208 were hardwired to StealthChop and during test prints the z axis stopped working. There is an discussion on Klipper's Git Repo: https://github.com/KevinOConnor/klipper/issues/196
    However, TMC2100 set to 16uSteps (256uSteps interpolation) and spreadCycle seems to work fine.
    [printer.cfg]
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2019-07-07 Updated design
    - Electronic compartment base for v6.x and v7 end effectors updated
    [electric_compartment_base_for_v6.x.stl, electric_compartment_base_for_v7.stl, electric_compartment_for_v6.x.f3d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]
2020-06-19 Added Klipper configurations for Carbonoid D1 #0003 & #0004
    [printer.cfg]
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2021-11-14 Added Klipper configuration for Carbonoid D1 #0002
    Controller Board: Panucat Azteeg X5 mini V3
    Display: Panucatt Viki 2 GLCD
    Steppers XYZ: TMC2208 @ 16 usteps
    Stepper E: TMC2100 @ 4 usteps
    Compile Target: LPC176x (120MHz)
    [printer.cfg]
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2021-11-15 Added design for improved "universal" electric compartment for the Carbonoid End Effector V7
    [electric_compartment_base_v8_f3d_universal.stl, electric_compartment_top_f3d_g4.stl, electric_compartment_top_f3d_g5.stl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]
2022-07-22 HW and FW updated.
    Changed Extruder from Flex3Drive G5 back to Bondtech QR Bowden Setup.
    Updated Klipper to latest version.
    [printer.cfg]
2024-11-19 Updated D1#0003
    - Switched from Octoprint to fluidd
    - Upated raspberry os to "bookworm"
    - Flashed C3D board with latest Klipper release
    [printer.cfg]
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2024-12-02 Added End Effector Design V10
    This new end effector supports the LDO Orbiter V2.x direct extruder. In combination with the Orbiter Toolboard this allows for a complete remote toolhead setup. There are two versions of the end effe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
    [electric_compartment_base_v8_f3d_universal.stl, electric_compartment_top_f3d_g4.stl, electric_compartment_top_f3d_g5.stl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]
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2024-12-13 Corrected inner diameter of parts to 22.6mm
    [RoofBaseGlue.stl, RoofBaseSolid.stl, roof.f3d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]
2024-12-13 Minor corrections
    [LowerCornerGlue.stl, LowerCornerSolid.stl, lower_corner.f3d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]
2024-12-13 Minor corrections of compression lid's inner diameter to 22.6mm
    [compression_lid_22_mm.stl, lids.f3d, lids.iges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]
2024-12-13 Minor correction in hole diameters.
    [MiddleCornerGlue.stl, MiddleCornerSolid.stl, middle_corner.f3d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]
2024-12-13 minor corrections in hole diameters.
    [LowerCornerGlue.stl, LowerCornerSolid.stl, lower_corner.f3d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]
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2024-12-16 Added new side cover with integrated mounting hole for a mini toggle switch.
    [side_cover_switch.stl, side_covers.f3d, side_covers.iges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]
2024-12-28 Removed inner cable channel from LowerCornerGlue as it is not needed anymore and only prolongs print time.
    [LowerCornerGlue.stl, lower_corner.f3d, lower_corner.iges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]
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2025-01-01 Added special version for D1 #0003 which uses different tower linear rods with M4 screws.
    Added special version for D1 #0003 which uses different tower linear rods with M4 screws.
    renamed stl files
    [MiddleCornerGlue.stl, MiddleCornerGlue_0003.stl, middle_corner.f3d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]
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2025-01-04 Optimized part so that it works holding the two F624ZZ bearings without additional washers.
    [belt_tensioner_F624ZZ.f3d, belt_tensioner_F624ZZ.iges, belt_tensioner_F624ZZ.step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]
2025-01-05 Updated design: Added variant of the lid with a PG7 cable gland.
    [electronic_compartment_lid_orbiter.stl, electronic_compartment_lid_orbiter_PG7.stl, electronic_compartment_lid_orbiter_PG9.stl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]
2025-01-07 Initial config after #0002 complete rebuilt and upgrade of the controller boards.
    [btt_ebb36_toolboard.cfg, printer.cfg]
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2025-01-10 Update after re-calibration. Arm length was wrong.
    [printer.cfg]
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2025-01-17 Added a variant of the V10 end effector with Neo Pixels for the Sherpa Mini V2 extruder.
    [end_effector_v10.stl, end_effector_v10_orbiter.stl, end_effector_v10_with_neo_pixels.stl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]
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2025-01-24 Updated configuration after final printer calibration and pid tuning of hotend & heated bed (280mm 220V Keenovo Heater).
    [printer.cfg]
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2025-01-29 Updated printer config after switching to 0.9deg stepper motors on ABC and installation of a new Keenovo Heater.
    [printer.cfg]
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2025-02-05 Added new configuration after upgrading D1 #0004 with a SherpaMiniV2 Direct Extruder, EBB36 Can Toolbpoard and E3D Revo Six hotend
    [btt_ebb36_toolboard.cfg, printer.cfg]
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2025-02-23 Added new configuration after upgrade of D1 #0003 with a SKR Pico Controller Board.
    [orbitool_o2.cfg, printer.cfg]
2025-02-25 Updated config after upgrading to SKR Pico and a 220V heated bed.
    [orbitool_o2.cfg, printer.cfg]
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
